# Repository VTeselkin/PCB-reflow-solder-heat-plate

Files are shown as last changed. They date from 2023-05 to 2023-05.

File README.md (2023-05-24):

# PCB reflow solder heat plate

## Introduction

The PCB reflow solder heat plate can be used to solder small PCBs with SMD parts. The user can control the maximum temperature and heating curve.

## Hardware design

The idea for this design comes from https://github.com/DerSpatz/PCB-reflow-solder-heat-plate. This project is a logical continuation and development of the original idea of PCB reflow solder heat plate.

### Feature list

- PCB size 100x100mm, heat plate size 81x69mm
- DC barrel plug (5.5x2.5mm), runs with 12V/5A power supply
- resettable 5A PTC fuse
- inrush current limiter to protect power supply when capacitors are discharged
- 2.7mF input power filter for smooth current draw
- capacitor discharging resistors
- ATMEGA4809 MCU, can be programmed via UPDI header
- high power NMOS with gate driver circuit
- flyback diode connected to the heat plate
- AMS1117 LDO
- additional diodes for protection
- dual buttons
- status LED
- 0.91" OLED display
- temperature measurement through NTC thermistor 3950 10k
- optimization of control, refusal of double pressing of buttons
- change R10 from 4K7 to 10K

### Building your own

You can order almost all parts needed from LCSC/JLCPCB. Only the OLED display and the power supply need to be sourced elsewhere. The BOM includes LCSC part numbers for hand soldering and their automated SMT manufacturing. Minimal part size is 0805 and there's enough space between all solder pads, so hand soldering should be no problem if you have a steady hand. Hardest part will be the MCU, but this is hand solderable, too.

### Safety measures compared to the original design

The original design had a too low heat plate resistance, which caused very high current spikes when the heat plate was turned on. This should be filtered by PWM and the input capacitors, but the input capacitor in the original design was far too small (100µF). Because of this, the fuse always blew when the device was turned on, so eventually the fuse was removed again.
In my design I made the input capacitors 27 times larger to have a smoother current draw. I also added a fuse, and an inrush current limiter. After disconnecting the power supply, the output capacitors are quickly discharged to GND.
The original also had no gate driver, so the NMOS was only driven with logic levels. I added a simple NPN gate driver.
Switching inductive loads (like the long heat plate trace) causes voltage spikes. In the original design, the filtering was done with an ESD diode and a small capacitor. The usual way to filter these voltage spikes is a flyback diode.
The resistance of the heat plate was very low, so the current draw with 100% PWM duty cycle was very high. If the MCUs hangs up and the power MOSFET stays active, the original design could cause too much stress for the power supply. Furthermore, even with a hot heat plate, the resistance would still be so low that the board would draw more than 5A.
In my design, the heat plate resistance was chosen in a way that a hot heat plate will draw less than 5A, so it is much safer to run the new design, as it will automatically reach electrically safe working conditions.

## Firmware

The original firmware was reworked by Nathan Heidt (https://github.com/heidtn) and works mostly, only the temperature sensing is incorrect (as the firmware was written with an earlier board revision). So for now, you just need to unplug the device when the PCB that needed soldering is done. Also, the dual color LED is not yet included into the code, for now it just lights green to show power. And the buttons sometimes don't react properly.

Daniel Oltmanns (https://github.com/oltdaniel) is doing a rework of the firmware using platformio.

### To-do list for software:
- use of the dual color LED (green = power, orange = heating, red = hot)
- better temperature sensing
- better working buttons
- calibration function for the analog temperature sensor by taping a digital probe directly to the heat plate

Please note that I can only do hardware design, so I can't contribute anything to the software. 

### Programming the MCU

The MCU can be programmed with JTAG2UPDI (https://github.com/ElTangas/jtag2updi). For programming, you need an Arduino with ATMEGA328p (Uno or Nano), some wires, a 4.7k resistor and  a 10µF capacitor or 120 Ohm resistor to disable the auto-reset.

JCM from the Discord explained the process pretty good:

> 1. Download/Clone this project: https://github.com/ElTangas/jtag2updi and rename the folder "source" to "jtag2updi" (otherwise the Arduino IDE won't like it)
> 2. Open jtag2updi/jtag2updi.ino in your Arduino IDE
> 3. Configure the flasher options for your Arduino Nano and flash it
> 4. Connect D6 of your Arduino Nano over the 4.7kOhm resistor to the UPDI pin of the board and 5V to 5V and GND to 0V
> 5. Add the MegaCoreX hardware package to the Ardunio IDE (see https://github.com/MCUdude/MegaCoreX#how-to-install)
> 6. Install the Adafruit_GFX, Adafruit_SSD1306, DallasTemperature and Debounce2 libraries with the Library Manager (you might not need all of them depending on which firmware you plan to use)
> 7. Download and open the ino you want to upload to the ATMEGA4809 (https://github.com/DerSpatz/PCB-reflow-solder-heat-plate/blob/main/Firmware/pcb_reflow_fw/pcb_reflow_fw.ino)
> 8. Select the options for the programmer (Board: ATmega4809, Clock: Internal 16 MHz, BOD: 2.6V or 2.7V, EEPROM: retained, Pinout: 48 pin standard, Reset pin: Reset, no Bootloader) and select the port of your Ardunio Nano as Port
> 9. Select Burn Bootloader and see if it runs through
> 10. Temporarily disable auto reset for the Arduino Nano: https://playground.arduino.cc/Main/DisablingAutoResetOnSerialConnection/ (not sure if it's needed for the Nano, it was for my Mega)
> 11. Select Sketch > Upload using Programmer (normal Upload will not work)

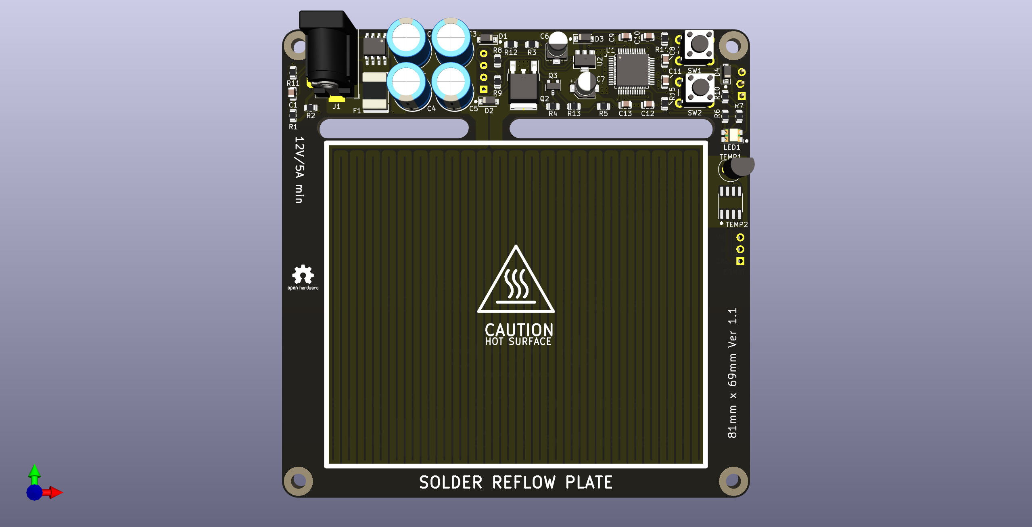
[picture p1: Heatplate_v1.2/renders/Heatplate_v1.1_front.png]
heatplate PCB front

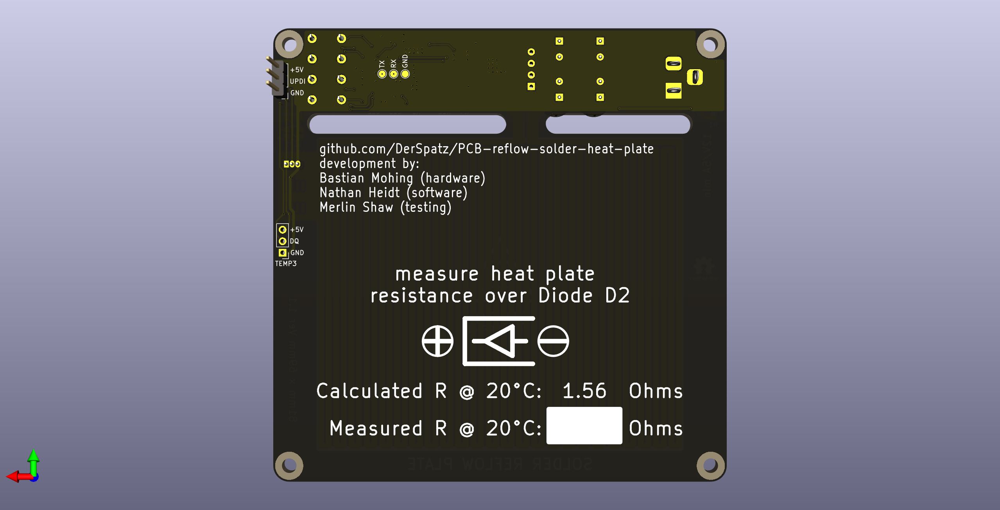
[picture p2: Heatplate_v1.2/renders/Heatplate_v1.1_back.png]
heatplate PCB back


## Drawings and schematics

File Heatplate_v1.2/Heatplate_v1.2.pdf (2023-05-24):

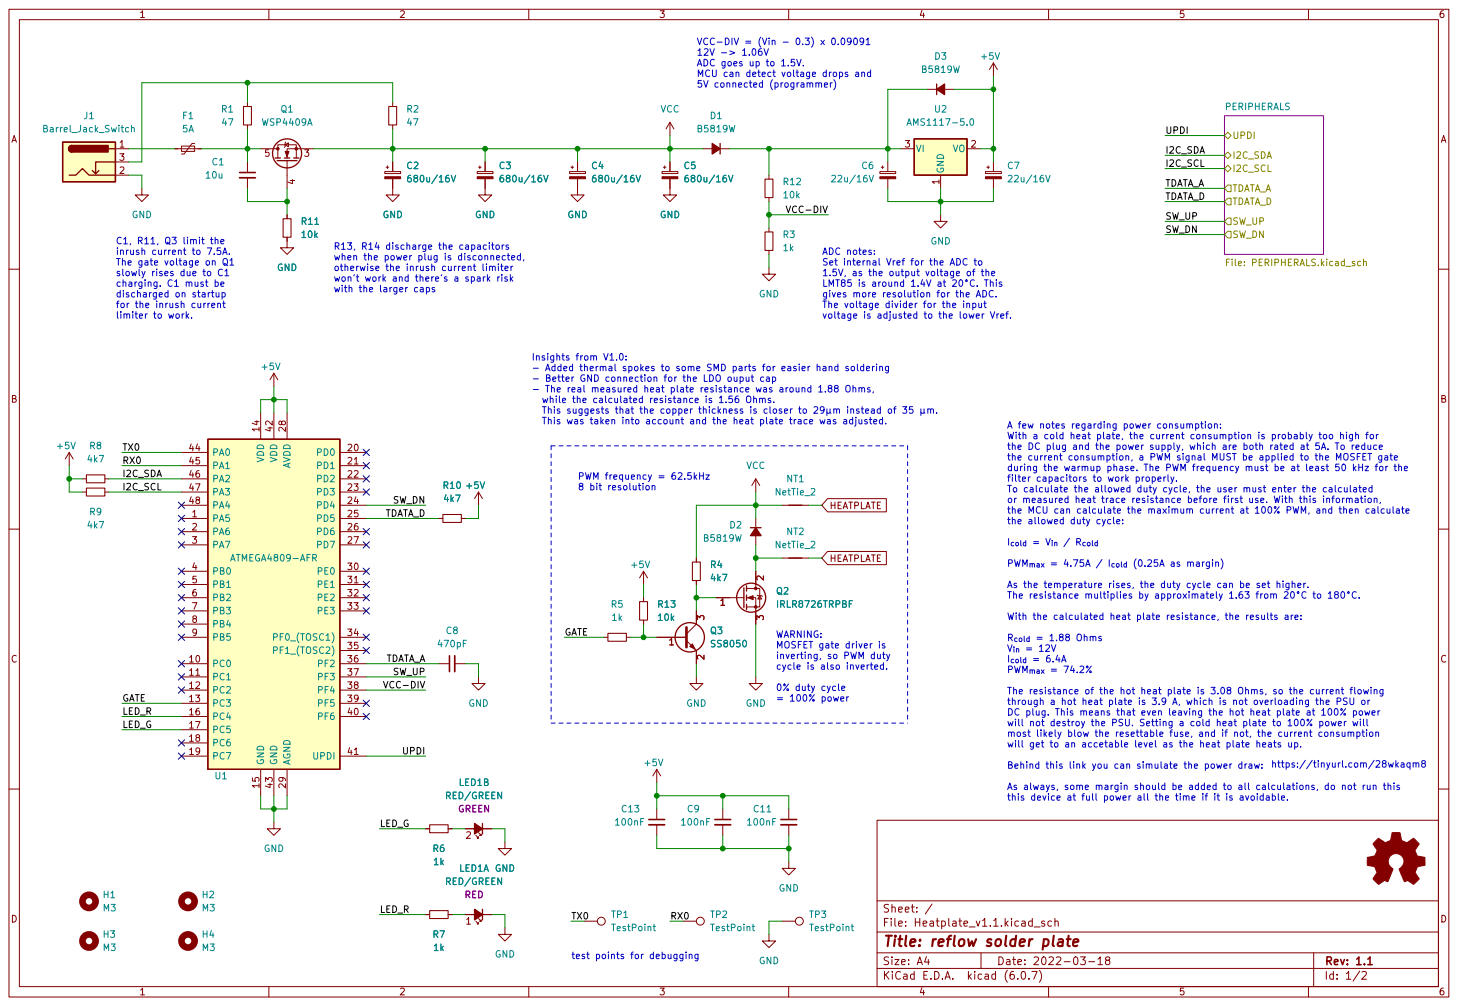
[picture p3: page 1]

VCC-DIV = (Vin - 0.3) x 0.09091
ADC goes up to 1.5V.
MCU can detect voltage drops and
5V connected (programmer)

R13, R14 discharge the capacitors
when the power plug is disconnected, otherwise the inrush current limiter won't work and there's a spark risk

This was taken into account and the heat plate trace was adjusted. C1, R11, Q3 limit the
inrush current to 7.5A. The gate voltage on Q1

ADC notes: Set internal Vref for the ADC to 1.5V, as the output voltage of the

slowly rises due to C1
charging. C1 must be
discharged on startup
for the inrush current
limiter to work.

with the larger caps

gives more resolution for the ADC.
The voltage divider for the input
voltage is adjusted to the lower Vref.

Insights from V1.0:
- Added thermal spokes to some SMD parts for easier hand soldering
- Better GND connection for the LDO ouput cap
- The real measured heat plate resistance was around 1.88 Ohms,
while the calculated resistance is 1.56 Ohms. þÿ  This suggests that the copper thickness is closer to 29µm instead of 35 µm.

A few notes regarding power consumption:
With a cold heat plate, the current consumption is probably too high for
the DC plug and the power supply, which are both rated at 5A. To reduce
the current consumption, a PWM signal MUST be applied to the MOSFET gate
during the warmup phase. The PWM frequency must be at least 50 kHz for the
filter capacitors to work properly.
To calculate the allowed duty cycle, the user must enter the calculated or measured heat trace resistance before first use. With this information,

PWM frequency = 62.5kHz 8 bit resolution

the MCU can calculate the maximum current at 100% PWM, and then calculate
the allowed duty cycle:

PWM_{max} = 4.75A / I_{cold} (0.25A as margin)

As the temperature rises, the duty cycle can be set higher.

With the calculated heat plate resistance, the results are:

this device at full power all the time if it is avoidable. WARNING: MOSFET gate driver is

inverting, so PWM duty
cycle is also inverted.

The resistance of the hot heat plate is 3.08 Ohms, so the current flowing
through a hot heat plate is 3.9 A, which is not overloading the PSU or
DC plug. This means that even leaving the hot heat plate at 100% power
will not destroy the PSU. Setting a cold heat plate to 100% power will
most likely blow the resettable fuse, and if not, the current consumption
will get to an accetable level as the heat plate heats up.

Behind this link you can simulate the power draw:

As always, some margin should be added to all calculations, do not run this

File: Heatplate_v1.1.kicad_sch Sheet: /
Id: 1/2 Title: reflow solder plate

test points for debugging

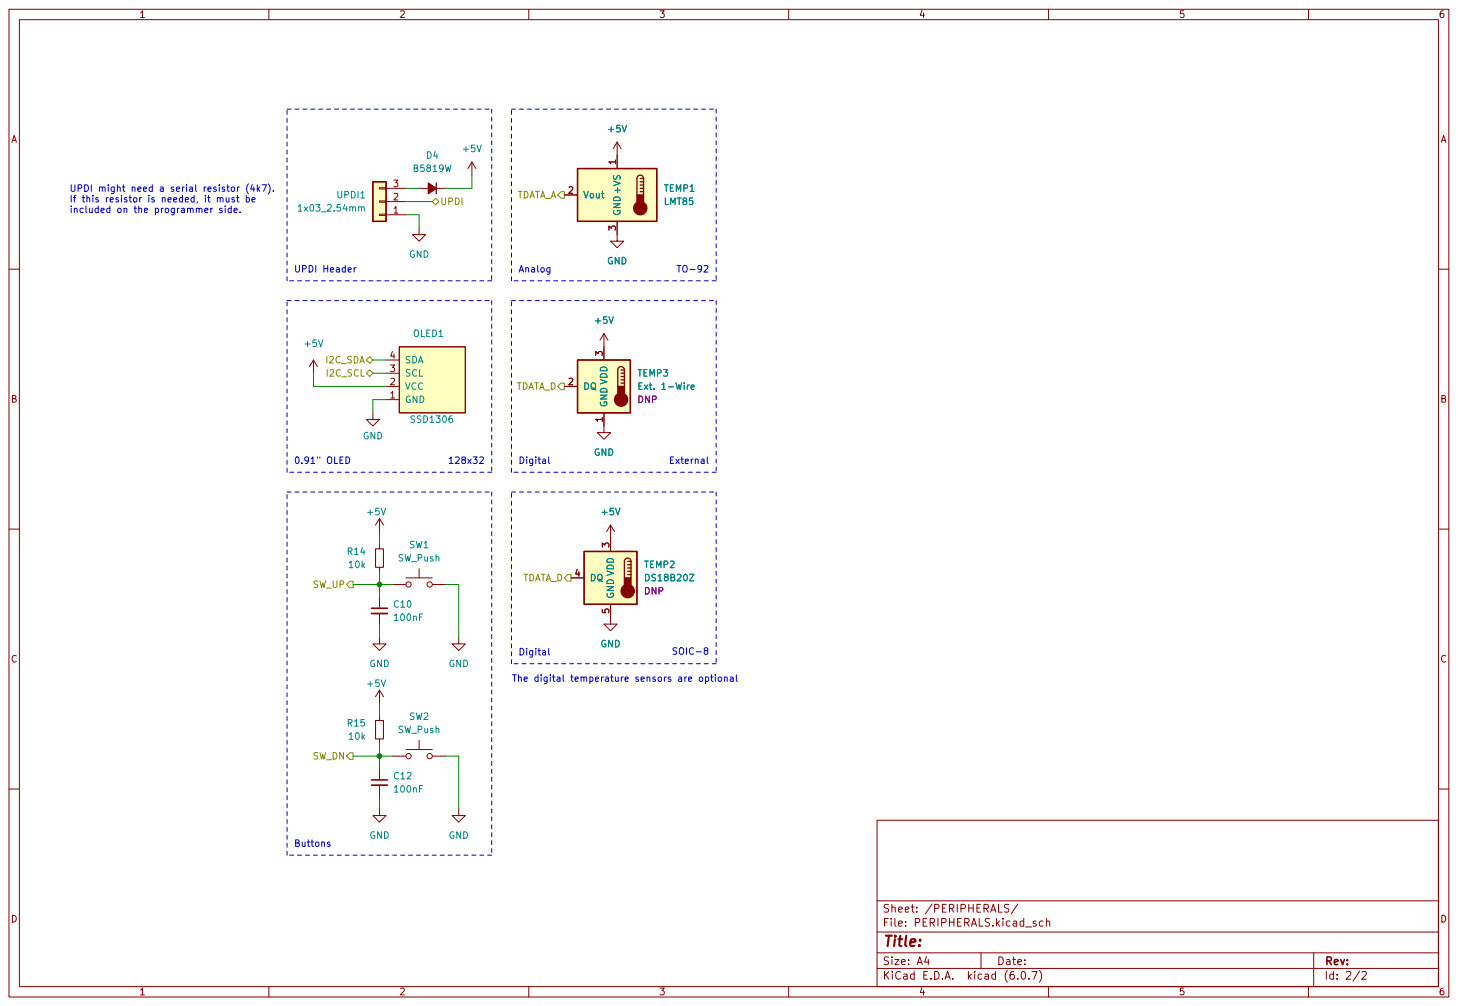
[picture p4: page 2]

UPDI might need a serial resistor (4k7).
If this resistor is needed, it must be

3 TEMP3 Ext. 1-Wire DNP VDD
TEMP3 Ext. 1-Wire DNP GND

File: PERIPHERALS.kicad_sch Sheet: /PERIPHERALS/ GND

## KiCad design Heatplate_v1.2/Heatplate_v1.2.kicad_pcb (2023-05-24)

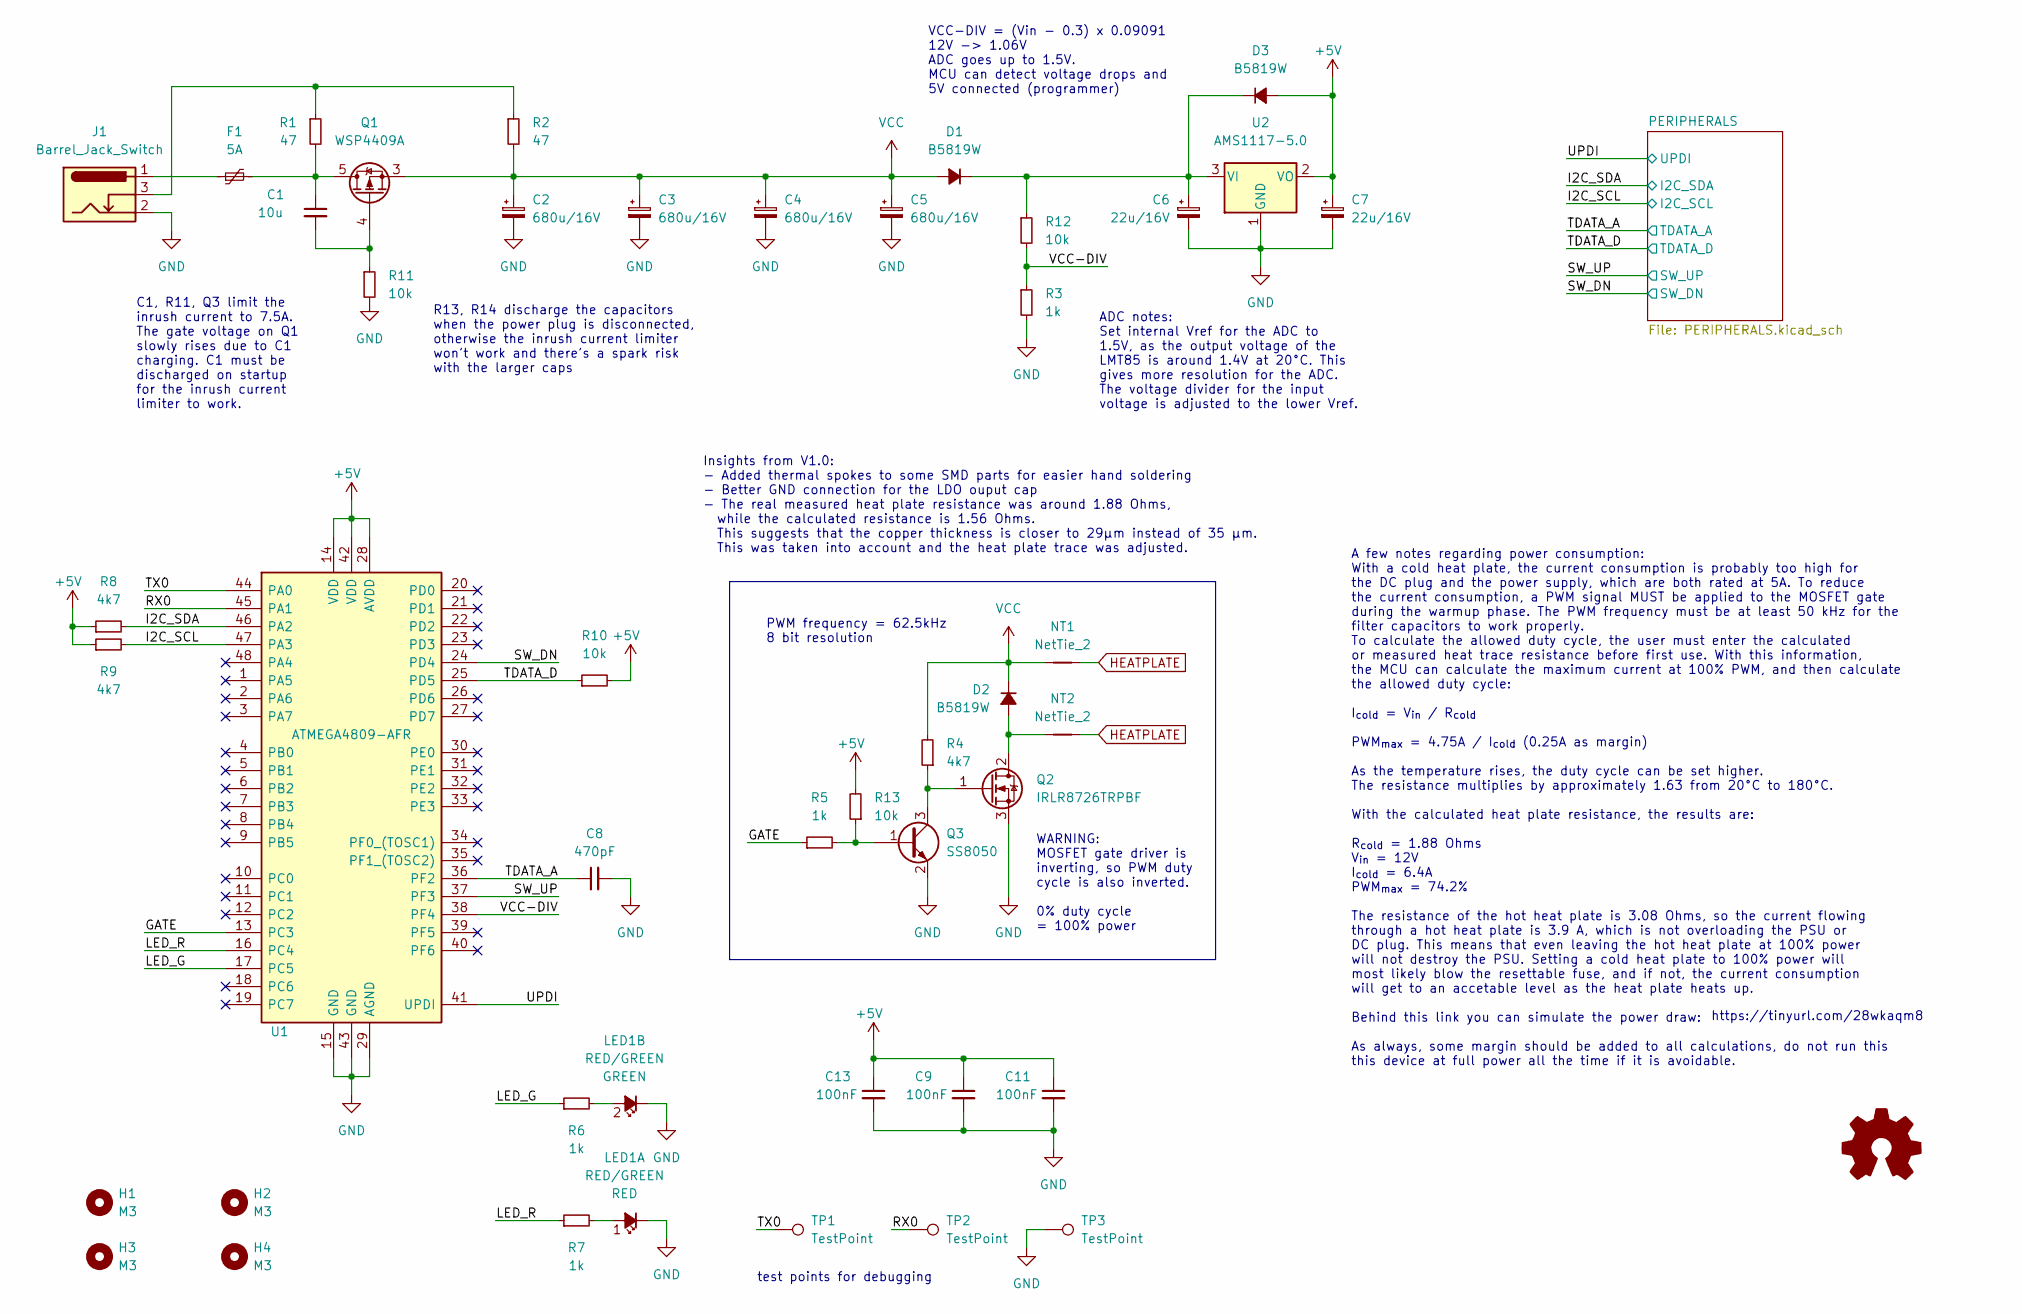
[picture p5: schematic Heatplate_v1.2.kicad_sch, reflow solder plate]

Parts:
C1: 10u; C_0805_2012Metric; LCSC Part Number C2922480
C2, C3, C4, C5: 680u/16V; CP_Radial_D8.0mm_P3.50mm; LCSC Part Number C88760
C6, C7: 22u/16V; CP_Elec_4x5.4; LCSC Part Number C88799
C8: 470pF; C_0805_2012Metric; LCSC Part Number C1743
C9, C11, C13: 100nF; C_0805_2012Metric; LCSC Part Number C1711
D1, D2, D3: B5819W; D_SOD-123; LCSC Part Number C64885
F1: 5A; Fuse_2920_7451Metric; LCSC Part Number C910846
H1, H2, H3, H4: M3; MountingHole_3.2mm_M3; LCSC Part Number C551332
J1: Barrel_Jack_Switch; BarrelJack_Horizontal; LCSC Part Number C381115
LED1: RED/GREEN; LED_Avago_PLCC4_3.2x2.8mm_CW; LCSC Part Number C131251
LOGO1: Logo_Open_Hardware_Small; OSHW-Logo2_7.3x6mm_SilkScreen
NT1, NT2: NetTie_2; NetTie-2_SMD_Pad1.3mm
Q1: WSP4409A; SOIC-8_3.9x4.9mm_P1.27mm; LCSC Part Number C2880527
Q2: IRLR8726TRPBF; TO-252-2; LCSC Part Number C81137
Q3: SS8050; SOT-23; LCSC Part Number C444722
R1, R2: 47; R_0805_2012Metric; LCSC Part Number C17714
R3, R5, R6, R7: 1k; R_0805_2012Metric; LCSC Part Number C17513
R4, R8, R9: 4k7; R_0805_2012Metric; LCSC Part Number C17673
R10: 10k; R_0805_2012Metric; LCSC Part Number C17673
R11, R12, R13: 10k; R_0805_2012Metric; LCSC Part Number C17414
TP1, TP2, TP3: TestPoint; TestPoint_Pad_D1.5mm
U1: ATMEGA4809-AFR; TQFP-48_7x7mm_P0.5mm; Manufacturer_Part_Number ATMEGA4809-AFR; Mouser Part Number 556-ATMEGA4809-AFR
U2: AMS1117-5.0; SOT-89-3; LCSC Part Number C351450

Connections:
+5V: C7.1, C9.1, C11.1, C13.1, D3.2 (A), R8.1, R9.1, R10.2, R13.2, U1.14 (VDD), U1.28 (AVDD), U1.42 (VDD), U2.2 (VO); also elsewhere on the board
/GATE: R5.1, U1.13 (PC3)
/I2C_SCL: R9.2, U1.47 (PA3); also elsewhere on the board
/I2C_SDA: R8.2, U1.46 (PA2); also elsewhere on the board
/LED_G: R6.1, U1.17 (PC5)
/LED_R: R7.1, U1.16 (PC4)
/RX0: TP2.1, U1.45 (PA1)
/SW_DN: U1.24 (PD4); also elsewhere on the board
/SW_UP: U1.37 (PF3); also elsewhere on the board
/TDATA_A: C8.1, U1.36 (PF2); also elsewhere on the board
/TDATA_D: R10.1, U1.25 (PD5); also elsewhere on the board
/TX0: TP1.1, U1.44 (PA0)
/UPDI: U1.41 (UPDI); also elsewhere on the board
/VCC-DIV: R3.1, R12.2, U1.38 (PF4)
GND: C2.2, C3.2, C4.2, C5.2, C6.2, C7.2, C8.2, C9.2, C11.2, C13.2, J1.2, LED1.2 (K1), LED1.4 (K2), Q2.3 (S), Q3.2 (E), R3.2, R11.2, TP3.1, U1.15 (GND), U1.29 (AGND), U1.43 (GND), U2.1 (GND); also elsewhere on the board
HEATPLATE: NT1.2, NT2.2
unnamed: C1.1, F1.2, Q1.5 (D), Q1.6 (D), Q1.7 (D), Q1.8 (D), R1.2
unnamed: C1.2, Q1.4 (G), R11.1
unnamed: C6.1, D1.1 (K), D3.1 (K), R12.1, U2.3 (VI)
unnamed: D2.2 (A), NT2.1, Q2.2 (D)
unnamed: F1.1, J1.1
unnamed: J1.3, R1.1, R2.1
unnamed: LED1.1 (A1), R7.2
unnamed: LED1.3 (A2), R6.2
unnamed: Q2.1 (G), Q3.3 (C), R4.1
unnamed: Q3.1 (B), R5.2, R13.1
VCC: C2.1, C3.1, C4.1, C5.1, D1.2 (A), D2.1 (K), NT1.1, Q1.1 (S), Q1.2 (S), Q1.3 (S), R2.2, R4.2

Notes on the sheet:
C1, R11, Q3 limit the inrush current to 7.5A. The gate voltage on Q1 slowly rises due to C1 charging. C1 must be discharged on startup for the inrush current limiter to work.
VCC-DIV = (Vin - 0.3) x 0.09091 12V -> 1.06V ADC goes up to 1.5V. MCU can detect voltage drops and 5V connected (programmer)
PWM frequency = 62.5kHz 8 bit resolution
A few notes regarding power consumption: With a cold heat plate, the current consumption is probably too high for the DC plug and the power supply, which are both rated at 5A. To reduce the current consumption, a PWM signal MUST be applied to the MOSFET gate during the warmup phase. The PWM frequen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
WARNING: MOSFET gate driver is inverting, so PWM duty cycle is also inverted. 0% duty cycle = 100% power
R13, R14 discharge the capacitors when the power plug is disconnected, otherwise the inrush current limiter won't work and there's a spark risk with the larger caps
https://tinyurl.com/28wkaqm8
test points for debugging
ADC notes: Set internal Vref for the ADC to 1.5V, as the output voltage of the LMT85 is around 1.4V at 20°C. This gives more resolution for the ADC. The voltage divider for the input voltage is adjusted to the lower Vref.
Insights from V1.0: - Added thermal spokes to some SMD parts for easier hand soldering - Better GND connection for the LDO ouput cap - The real measured heat plate resistance was around 1.88 Ohms, while the calculated resistance is 1.56 Ohms. This suggests that the copper thickness is closer to 29µ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

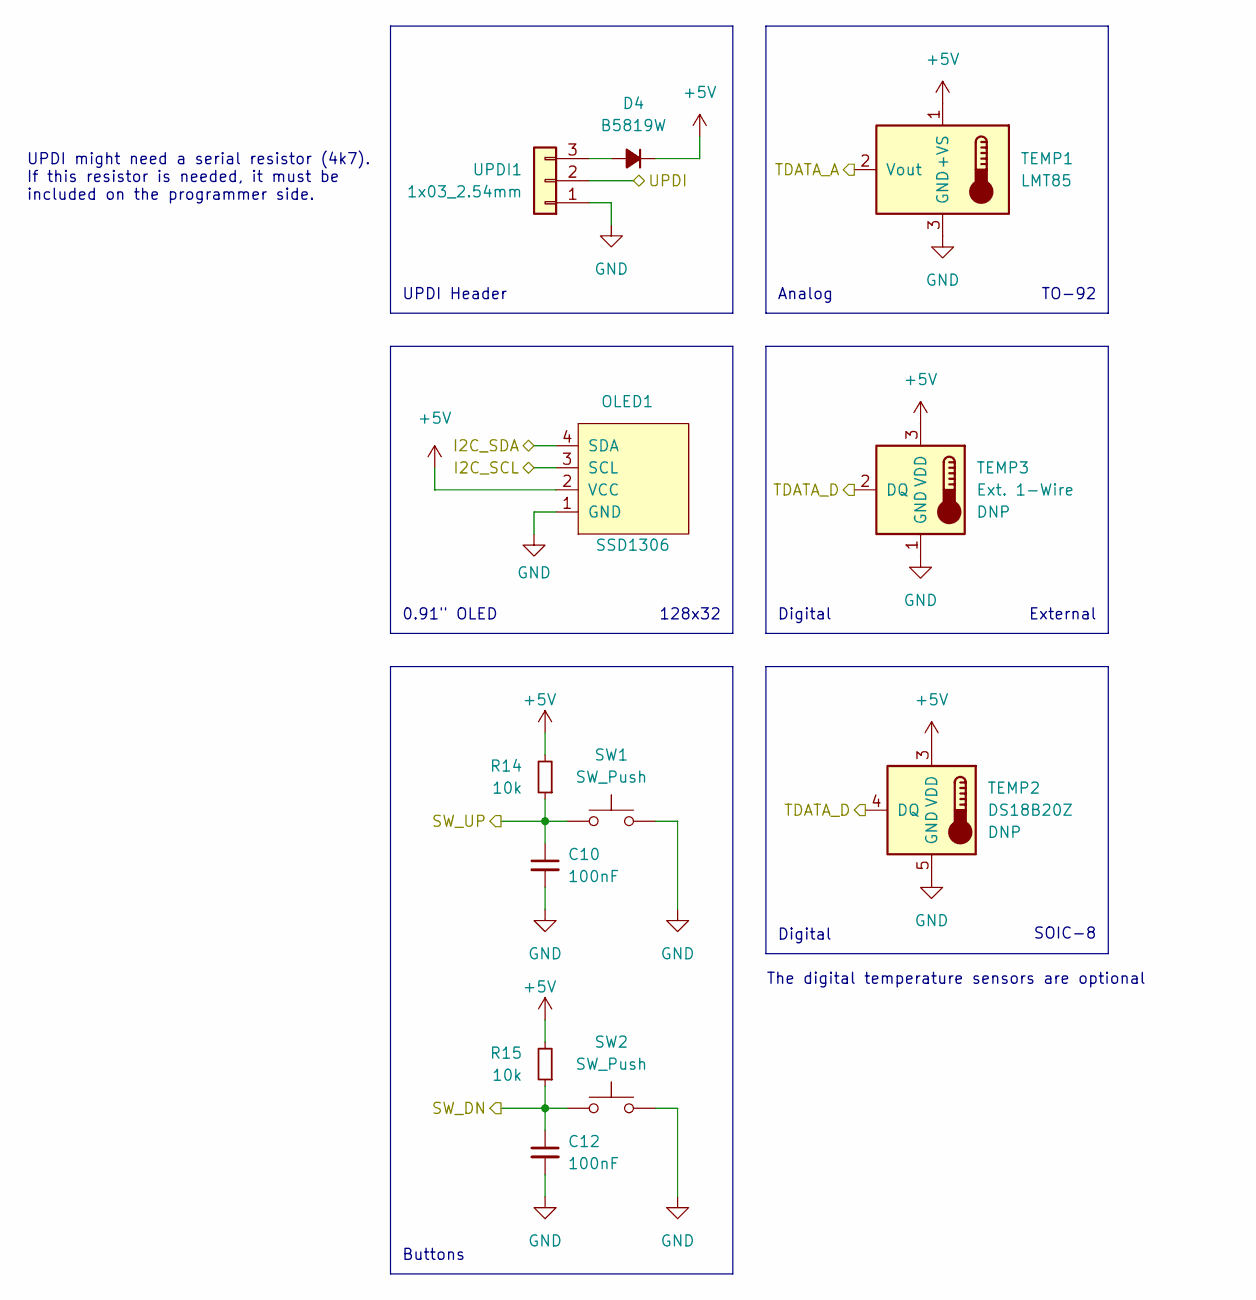
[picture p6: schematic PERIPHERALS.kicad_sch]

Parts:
C10, C12: 100nF; C_0805_2012Metric; LCSC Part Number C1711
D4: B5819W; D_SOD-123; LCSC Part Number C64885
OLED1: SSD1306; 0.91Inch-OLED-Module; LCSC Part Number C2718488
R14, R15: 10k; R_0805_2012Metric; LCSC Part Number C17414
SW1, SW2: SW_Push; SW_PUSH_6mm; LCSC Part Number C136682
TEMP1: LMT85; TO-92_Inline; LCSC Part Number C75856
TEMP2: DS18B20Z; SOIC-8_3.9x4.9mm_P1.27mm; LCSC Part Number C695837
TEMP3: Ext. 1-Wire; PinHeader_1x03_P2.54mm_Vertical
UPDI1: 1x03_2.54mm; PinHeader_1x03_P2.54mm_Vertical; LCSC Part Number C49257

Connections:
+5V: D4.1 (K), OLED1.2 (VCC), R14.2, R15.2, TEMP1.1 (+VS), TEMP2.3 (VDD), TEMP3.3 (VDD); also elsewhere on the board
/I2C_SCL: OLED1.3 (SCL); also elsewhere on the board
/I2C_SDA: OLED1.4 (SDA); also elsewhere on the board
/SW_DN: C12.1, R15.1, SW2.1; also elsewhere on the board
/SW_UP: C10.1, R14.1, SW1.1; also elsewhere on the board
/TDATA_A: TEMP1.2 (Vout); also elsewhere on the board
/TDATA_D: TEMP2.4 (DQ), TEMP3.2 (DQ); also elsewhere on the board
/UPDI: UPDI1.2; also elsewhere on the board
GND: C10.2, C12.2, OLED1.1 (GND), SW1.2, SW2.2, TEMP1.3 (GND), TEMP2.5 (GND), TEMP3.1 (GND), UPDI1.1; also elsewhere on the board
unnamed: D4.2 (A), UPDI1.3

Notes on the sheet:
SOIC-8
Digital
UPDI Header
128x32
Analog
TO-92
0.91" OLED
The digital temperature sensors are optional
Buttons
UPDI might need a serial resistor (4k7). If this resistor is needed, it must be included on the programmer side.
External

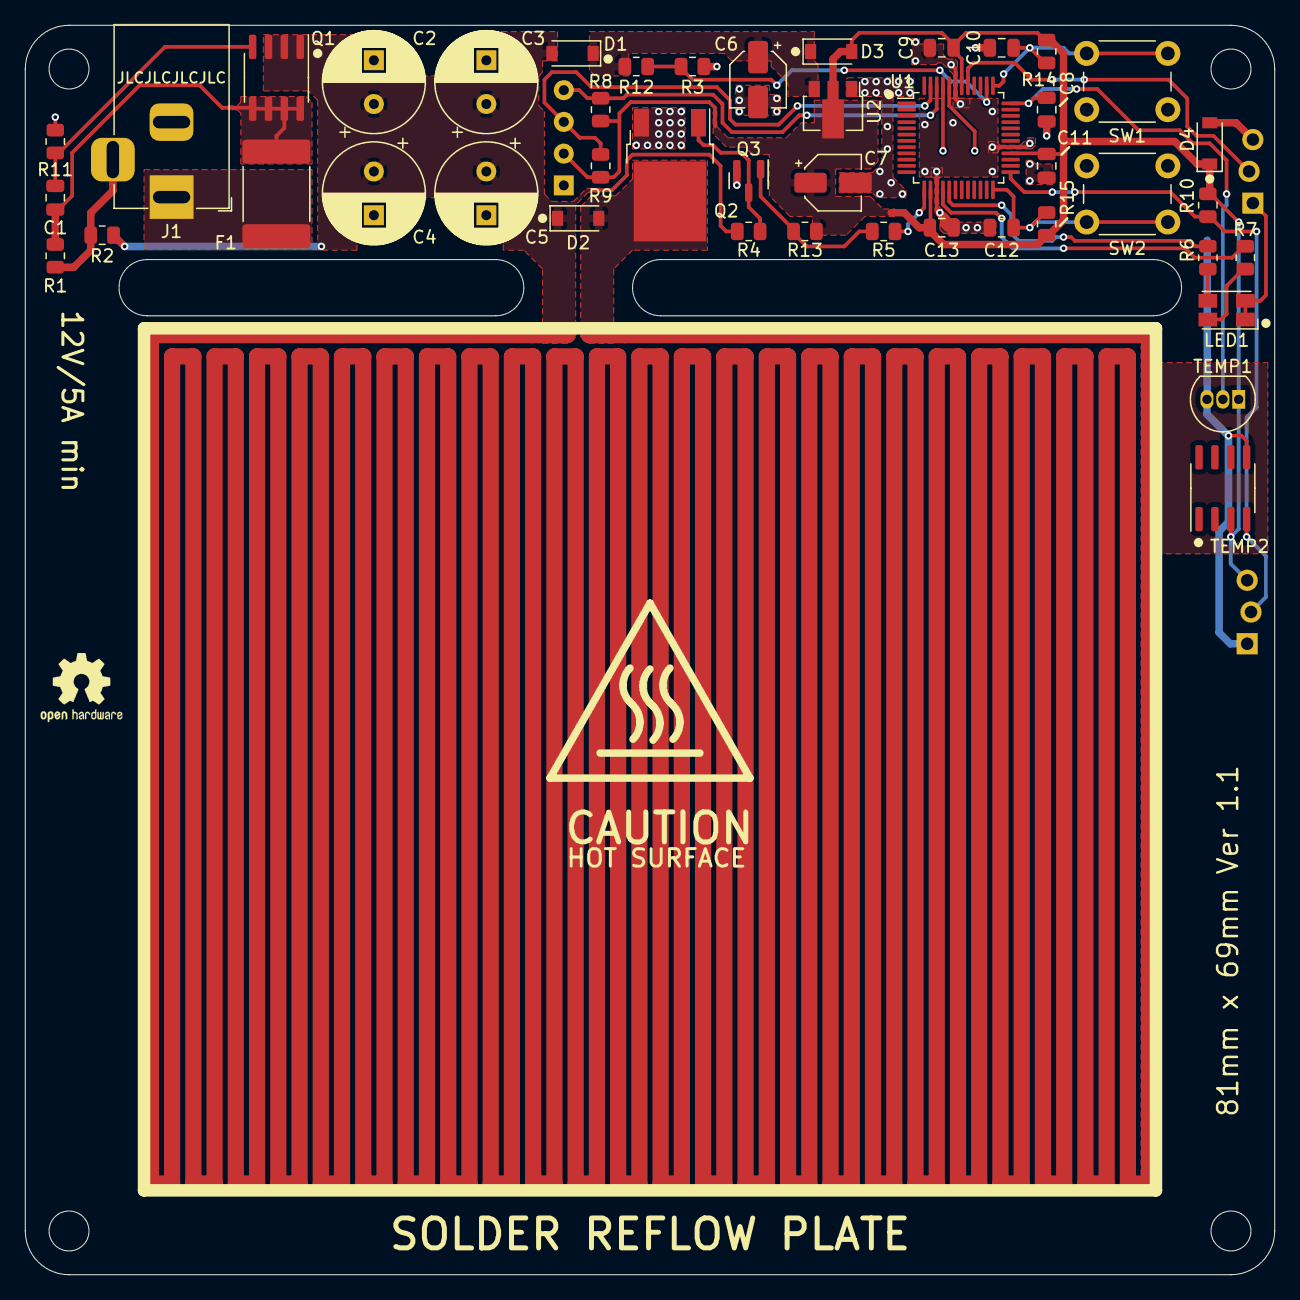
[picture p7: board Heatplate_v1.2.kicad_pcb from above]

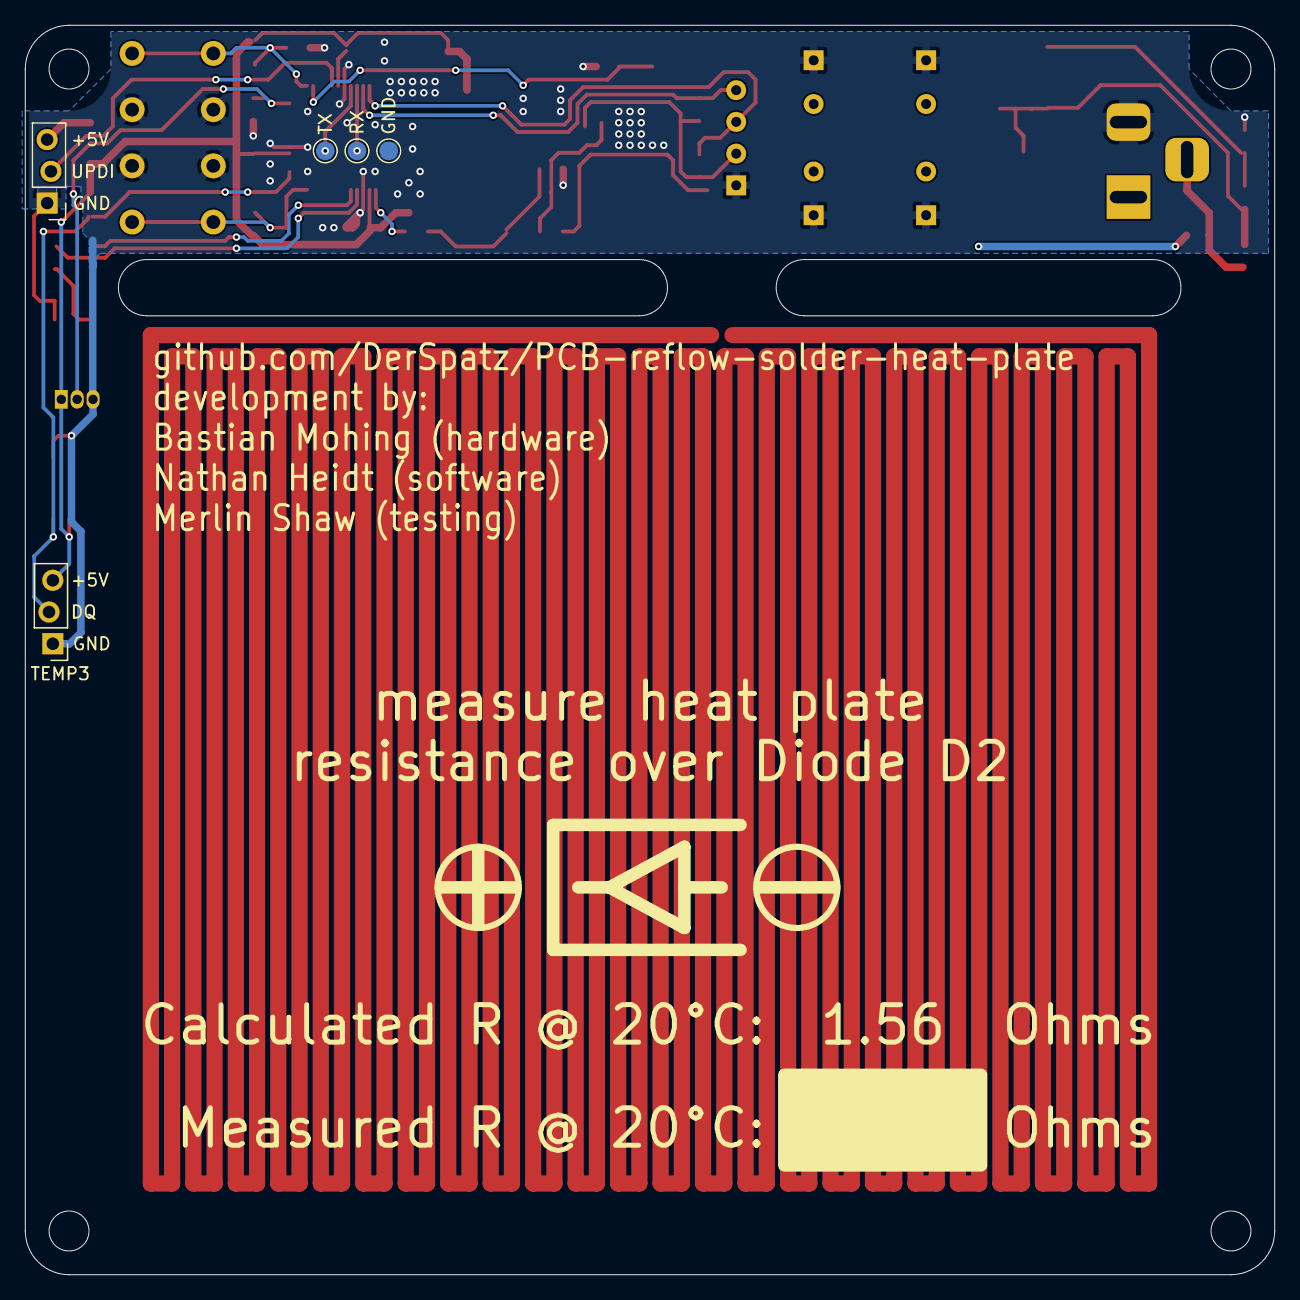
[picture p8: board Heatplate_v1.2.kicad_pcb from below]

Board: 2 copper layers, 100.0 x 100.0 mm, 57 parts (5 on the bottom side), 28 nets.

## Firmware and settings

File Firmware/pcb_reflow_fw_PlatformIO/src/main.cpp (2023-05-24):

/* Solder Reflow Plate Sketch
 *  H/W - Ver Spatz-1.0
 *  S/W - Ver 0.35
 *  by Chris Halsall and Nathan Heidt
 */

/*
 * TODOS:
 * - add digital sensor setup routine if they are detected, but not setup
 * - figure out a method for how to use all the temperature sensors
 * - implement an observer/predictor for the temperature sensors.  Kalman filter
 * time?!?
 */

#include <display.h>
#include <heater.h>
#include <controll.h>
#include <helpers.h>
#include <debug.h>
#include <preference.h>

#include <SimpleKalmanFilter.h>

Display display;
Controll controll;
Preference preference;
Heater heater;
Debug debug;

int profile_index = 0;

void mainMenu();
void doSetup();
float getTempCallBack();
void cancelledTimerCallBack();
buttons_state_t getButtonsStateCallBack();
void showHeatMenuCallBack(float max_temp);
void heatAnimateCallBack(int x, int y, float v, float t, float target);

void setup()
{
  // Pin Direction control
  pinMode(MOSFET_PIN, OUTPUT);
  pinMode(UPSW_PIN, INPUT);
  pinMode(DNSW_PIN, INPUT);
  pinMode(TEMP_PIN, INPUT);
  pinMode(VCC_PIN, INPUT);
  pinMode(LED_GREEN_PIN, OUTPUT);
  pinMode(LED_RED_PIN, OUTPUT);

  digitalWrite(LED_GREEN_PIN, LOW);
  digitalWrite(LED_RED_PIN, LOW);

  controll.setLedState(LED_GREED, true);

  analogWrite(MOSFET_PIN, 255); // VERY IMPORTANT, DONT CHANGE!

  attachInterrupt(DNSW_PIN, controll.dnsw_change_isr, FALLING);
  attachInterrupt(UPSW_PIN, controll.upsw_change_isr, FALLING);

  debug.setup();

  // Enable Fast PWM with no prescaler
  analogWriteFrequency(64);
  // analogReference(DEFAULT);

  // Start-up Diplay
  debugprintln("Showing startup");
  display.showLogo(doSetup, getButtonsStateCallBack);

  debugprintln("Checking sensors");
  // check onewire TEMP_PIN sensors
  heater.setupSensors();

  debugprintln("Checking first boot");
  if (preference.isFirstBoot() || !preference.validateCRC())
  {
    doSetup();
  }

  // Pull saved values from EEPROM
  max_temp_index = preference.getMaxTempIndex();
  bed_resistance = preference.getResistance();

  debugprintln("Entering main menu");
  // Go to main menu
  mainMenu();
}

void loop()
{
  // Not used
}

void mainMenu()
{
  // Debounce
  menu_state_t cur_state = MENU_IDLE;

  int x = 0;   // Display change counter
  int y = 200; // Display change max (modulused below)

  while (1)
  {
    switch (cur_state)
    {
    case MENU_IDLE:
    {
      display.clearMainMenu();
      controll.setLedState(LED_GREED, false);
      controll.setLedState(LED_RED, false);
      buttons_state_t cur_button = controll.getButtonsState();

      if (cur_button == BUTTONS_UP_PRESS)
      {
        cur_state = MENU_INC_TEMP;
      }
      else if (cur_button == BUTTONS_DN_PRESS)
      {
        cur_state = MENU_SELECT_PROFILE;
      }
    }
    break;
    case MENU_SELECT_PROFILE:
    {
      debugprintln("getting thermal profile");
      profile_index = display.getProfile(getButtonsStateCallBack);
      cur_state = MENU_HEAT;
    }
    break;
    case MENU_HEAT:
    {
      controll.setLedState(LED_RED, true);
      controll.setLedState(LED_GREED, false);
      if (!heater.heat(showHeatMenuCallBack, getButtonsStateCallBack,
                       cancelledTimerCallBack, heatAnimateCallBack,
                       max_temp_array[max_temp_index], profile_index))
      {
        display.cancelledPB();
        display.coolDown(getTempCallBack, getButtonsStateCallBack);
        controll.setLedState(LED_RED, false);
        controll.setLedState(LED_GREED, true);
      }
      else
      {
        display.coolDown(getTempCallBack, getButtonsStateCallBack);
        display.completed(getButtonsStateCallBack);
        controll.setLedState(LED_RED, false);
        controll.setLedState(LED_GREED, false);
      }
      cur_state = MENU_IDLE;
    }
    break;
    case MENU_INC_TEMP:
    {
      debugprintln("incrementing max temp");
      if (max_temp_index < sizeof(max_temp_array) - 1)
      {
        max_temp_index++;
      }
      else
      {
        max_temp_index = 0;
      }
      preference.setMaxTempIndex(max_temp_index);
      cur_state = MENU_IDLE;
    }
    break;
    }

    // Change Display (left-side)
    display.showMainMenuLeft(x, y);

    // Update Display (right-side)
    display.showMainMenuRight(max_temp_index);
  }
}

void doSetup()
{
  debugprintln("Performing setup");
  // TODO(HEIDT) show an info screen if we're doing firstime setup or if memory
  // is corrupted

  display.getResistanceFromUser(preference, getButtonsStateCallBack);
  // TODO(HEIDT) do a temperature module setup here

  preference.setFirstBoot();
}

//----------------------- call back region ---------------------------//

float getTempCallBack()
{
  return heater.getTemp();
}

buttons_state_t getButtonsStateCallBack()
{
  return controll.getButtonsState();
}

void showHeatMenuCallBack(float max_temp)
{
  display.showHeatMenu(max_temp);
}

void cancelledTimerCallBack()
{
  display.cancelledTimer(getButtonsStateCallBack);
}

void heatAnimateCallBack(int x, int y, float v, float t, float target)
{
  display.heatAnimate(x, y, v, t, target);
}

//------------------------------------------------------------------//

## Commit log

2023-03-05 -add Heater lib
2023-03-06 -add Kalman Filter
2023-05-24 -add last changes
    [Heatplate_v1.2.kicad_pcb, Heatplate_v1.2.kicad_sch, PERIPHERALS.kicad_sch]
